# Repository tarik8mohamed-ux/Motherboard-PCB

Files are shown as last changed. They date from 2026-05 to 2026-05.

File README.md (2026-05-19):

# Hyperloop Motherboard PCB
Hyperloop Motherboard PCB Design (KiCad Schematics, component footprints, layouts, and diagrams)

Cornell Hyperloop SP'26
ECC:   Tarik, Peri, Farah, and Vinny

## Introduction: 
This project is a central control PCB designed to serve as the primary communication and motor control hub for Cornell Hyperloop's MiniPod. The board integrates multiple communication protocols to interface with a variety of peripherals: CANopen for servo motor control via the EPOS2 70/10, Step/Dir for stepper motor control via the TB6600, I2C for a distributed sensor network of temperature and current monitors, and PWM for fan speed control. The modular architecture supports hot-pluggable expansion, allowing sensors, MCU, and Multiplexers to be swapped or added without disrupting system operation. The board is ~265mm x 135mm and consists of 4 Layers: Signal-GND-PWR-Signal, with the PWR plane seperated into 3.3V,5.0V, and 12V sections to support different components. The most up to date files are in the Hyperloop Organized PCB folder.

Hyperloop PCB 3D View 2
Hyperloop PCB 3D View
Hyperloop PCB Planes View

## Components:
Cornell Hyperloop's MiniPod is ~7ft, meaning that sesnors and motors must be controlled by the motherbaord from a distance. This is why most components will be connected to the PCB via Cable/Wire connectors.
#### MCU:
The motherboard is controlled with an Arduino Nano R4
<table>
  <tr>
    <td align="center"><b>Arduino Nano R4</b></td>
  </tr>
  <tr>
    <td>1782_sml</td>
  </tr>
</table>

#### Sensors & Fan Control:
Overheating and current spikes are critical concerns on the Pod, so temperature and current sensors are distributed throughout. Temperature sensors use 8-pin Molex connectors (2 power, 2 communication, 1 interrupt, 3 alert pins), while current sensors use 4-pin Molex connectors (2 power, 2 communication pins). Vin+ and Vin− are connected across the points being measured, not the board, and I²C addresses are permanently hardset on the board. Additionally, a TCA9548A I2C multiplexer was integrated to expand the single I2C bus into up to 8 independent channels. 4-pin cooling fans are also distributed across the Pod, represented as 4-pin Molex connectors.
<table>
  <tr>
    <td align="center"><b>Temperature Sensor: MCP9808 </b></td>
    <td align="center"><b>Current Sensor: INA260</b></td>
    <td align="center"><b>Fan: Arctic P12</b></td>
    <td align="center"><b>Multiplexer: TCA9548A</b></td>
  </tr>
  <tr>
    <td></td>
    <td>1782_sml</td>
    <td>1782_sml</td>
    <td>1782_sml</td>
  </tr>
</table>

#### Motor Control:
The Pod interfaces with a TB6600 stepper driver and an EPOS2 70/10 servo controller. The TB6600 is controlled via Step/Dir/Enable signals through a Phoenix Contact screw terminal, and the EPOS2 communicates over CANopen through a Molex Micro-Fit 3.0 4-pin connector.
<table>
  <tr>
    <td align="center"><b>4-pin Pheonix Contact Screw Terminal</b></td>
    <td align="center"><b>Molex Micro-Fir 3.0 4-pin connector</b></td>
  </tr>
  <tr>
    <td></td>
    <td>1782_sml</td>
  </tr>
</table>

#### GPIO Expander:
An MCP23017 I2C expander is included to provide additional GPIO pins for the Pod as needed. Breakout headers expose all 16 I/O pins for flexible peripheral connections.
The motherboard is controlled with an Arduino Nano R4
<table>
  <tr>
    <td align="center"><b>MCP23017 I2C Expander:</b></td>
  </tr>
  <tr>
    <td>1782_sml</td>
  </tr>
</table>

#### Power, Resistors, Capacitors:
The PCB contains 3.3V,5.0V, and 12.0V sections in the power plane. XT30 connectors will be used to connect external battery packs to drive the power plane.
Resistors typically take on the role of pull-ups in this design. Through-Hole Resistors are used for ease of soldering. On the other hand, capacitors are typically used for bypass or decoupling. In this context, we picked SMD capacitors despite the extra difficulty in soldering because they significantly outperform THT.
<table>
  <tr>
    <td align="center"><b>XT30 Connector:</b></td>
  </tr>
  <tr>
    <td>1782_sml</td>
  </tr>
</table>

## Communication Systems:
### I2C Sensor Network & I2C Expander:
The I2C network, located in the top left of the PCB, is managed by a TCA9548A multiplexer which expands the microcontroller's single I2C bus into 4 independent channels, each with its own pull-up resistors to maintain signal integrity. Each channel hosts sensor peripherals, with every device supported by a dedicated decoupling capacitor for noise suppression. A series resistor on the main I2C line dampens inductive ringing before the signal reaches the multiplexer. MCP9808 temperature sensors feature an active-low alert pin connected to a microcontroller GPIO, enabling interrupt-driven temperature monitoring without continuous polling. An MCP23017 I2C I/O expander is also connected to the bus, currently populated with breakout headers for flexible future peripheral connections.

### CAN EPOS2 70/10:
CANopen communication is implemented using a TCAN332 transceiver, which converts the microcontroller's TX/RX signals into differential CANH/CANL signals. A 120Ω termination resistor is placed at the output connector to prevent signal reflections. The bus connects to an EPOS2 70/10 servo controller via a Molex Micro-Fit 3.0 cable. It is located below the MCU.

### Step/Dir TB6600:
The TB6600 stepper driver is controlled via three GPIO signals — PUL+, DIR+, and ENA+ — using a common-cathode wiring configuration. Series resistors on each line dampen signal ringing before reaching the Phoenix Contact screw terminal output connector. It is located just above the MCU.

### PWM Fan CTRL:
Two pairs of fans are controlled via PWM signals from the microcontroller, with each pair sharing a single PWM output to conserve GPIO pins. One tachometer signal per pair is routed back to a microcontroller GPIO, providing RPM feedback for monitoring fan speed. Each fan connector includes dedicated power and ground connections for reliable operation. It is located on the right side of the board.

## Future Updates
-INA260 Alert Pin: The INA260 current sensor connector will be expanded from 4 to 5 pins to expose the ALERT pin, enabling interrupt-driven current monitoring in place of polling across the I2C channels and significantly improving CPU efficiency.    

-TCAN332 Connector Orientation: The CAN connector will be changed from horizontal to vertical to improve accessibility and PCB layout clarity.

-Component Density: Component placement will be optimized for a smaller board footprint, reducing fabrication cost.

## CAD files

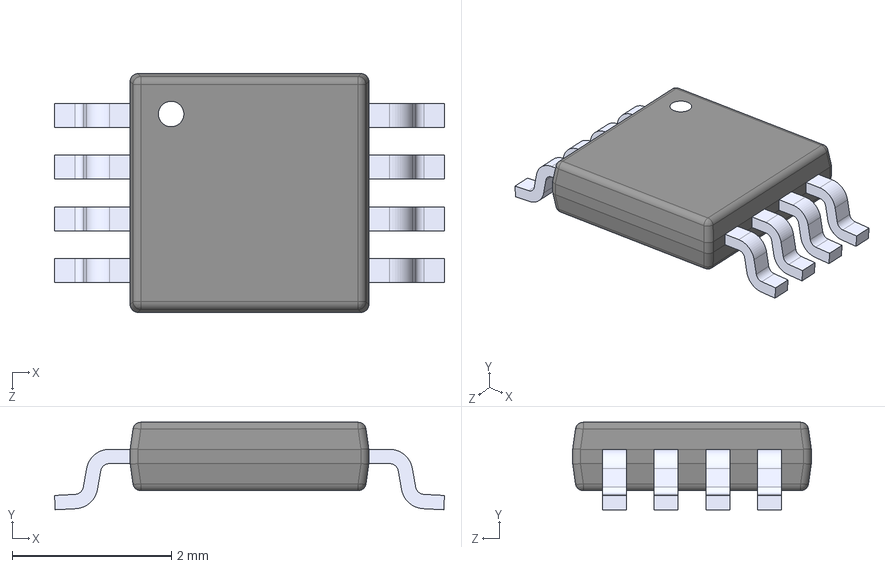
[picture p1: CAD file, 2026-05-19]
KiCad Components/KiCad 3D Models/LTC4446EMS8EPBF(MagBrake Driver).step
4.90 x 1.10 x 3.00 mm

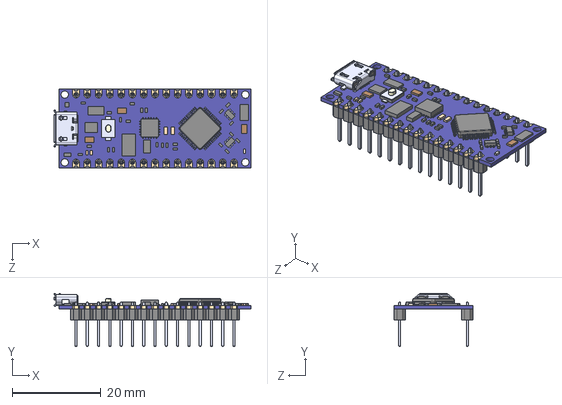
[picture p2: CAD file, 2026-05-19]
KiCad Components/KiCad 3D Models/Arduino_Nano_Every.STEP
44.3 x 12.0 x 17.8 mm

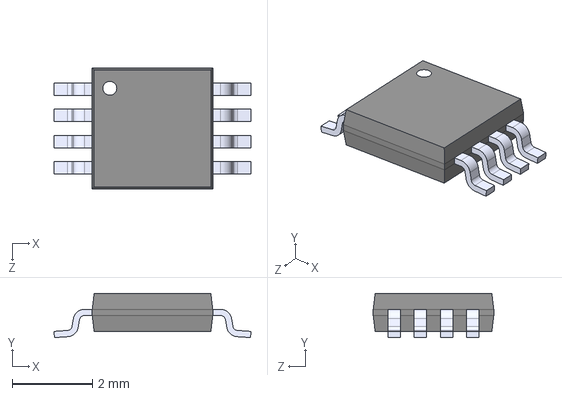
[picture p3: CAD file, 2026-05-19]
KiCad Components/KiCad 3D Models/MCP9808-E_MS(Temp Sensor).step
4.90 x 1.10 x 3.00 mm

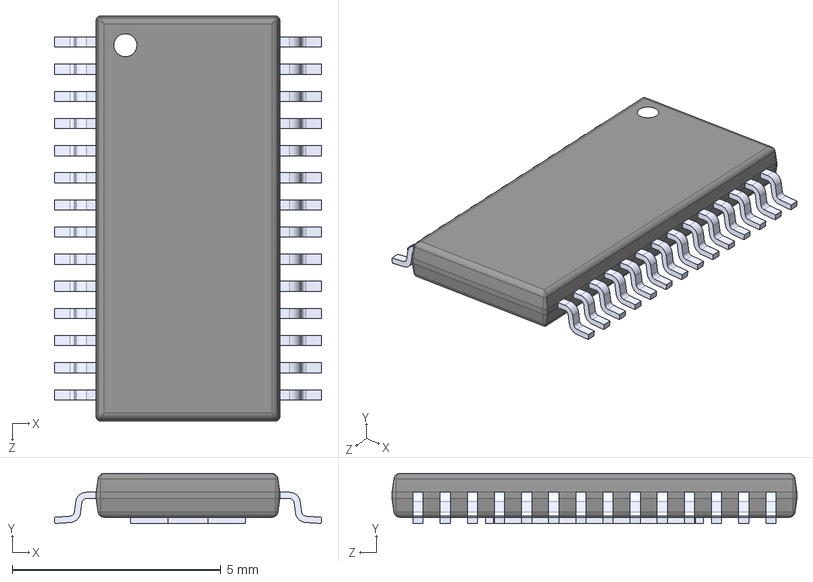
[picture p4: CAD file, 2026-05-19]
KiCad Components/KiCad 3D Models/DRV8424PWPR(Motor Driver).step
6.40 x 1.20 x 9.70 mm

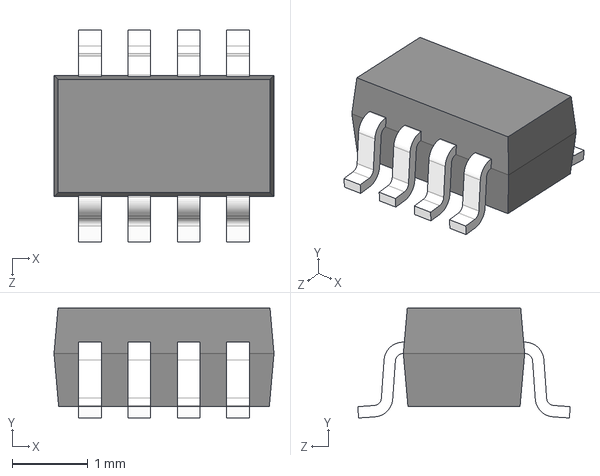
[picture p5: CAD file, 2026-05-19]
KiCad Components/KiCad 3D Models/INA219(Current Sensor).step
2.90 x 1.45 x 2.80 mm

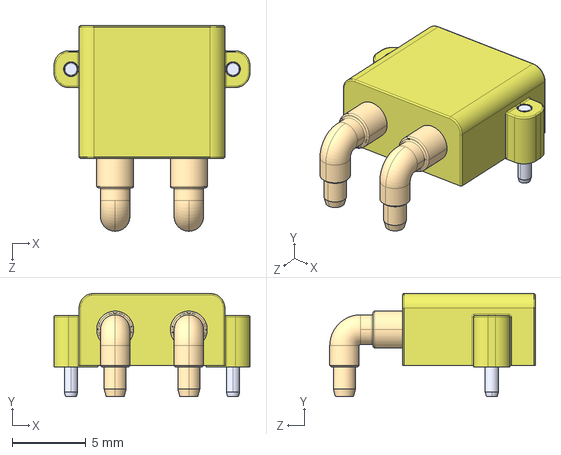
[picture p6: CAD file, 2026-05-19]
KiCad Components/KiCad 3D Models/XT30PW-M.step
13.3 x 7.00 x 14.0 mm

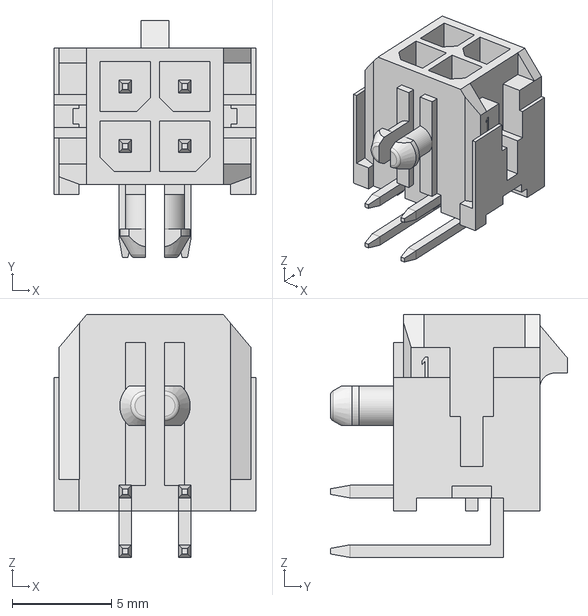
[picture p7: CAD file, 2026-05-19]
KiCad Components/KiCad 3D Models/TCAN_Connector(Horizontal).stp
10.2 x 11.9 x 12.2 mm

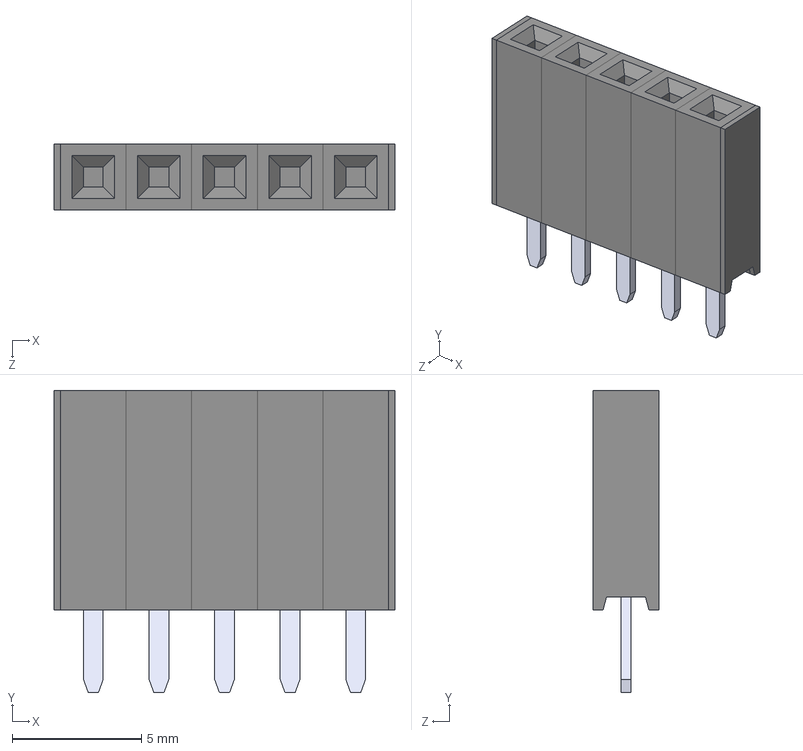
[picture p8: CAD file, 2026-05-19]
KiCad Components/KiCad 3D Models/5FemaleHeaderPins.STEP
13.2 x 11.7 x 2.54 mm
PPPC021LFBN-RC_C05
Pin - Tin x 5

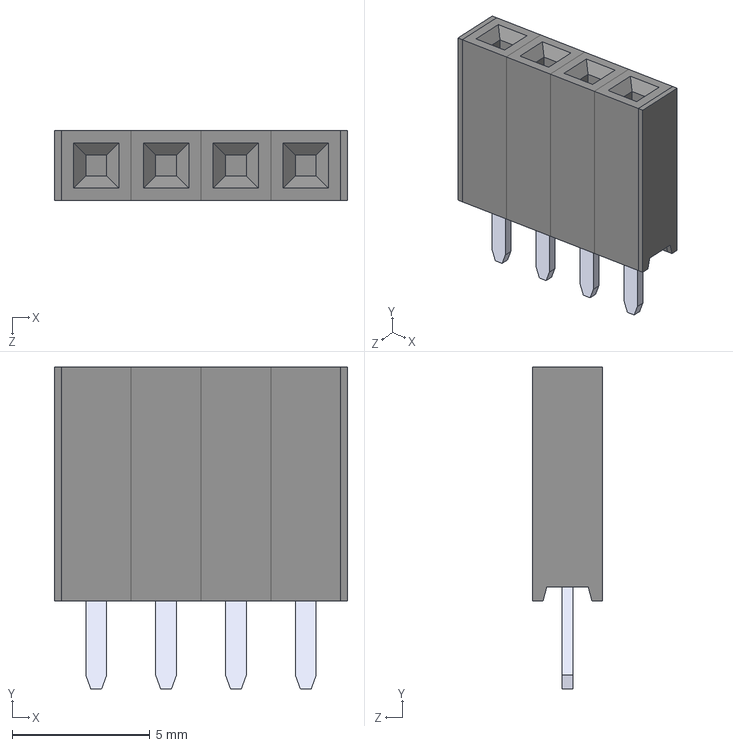
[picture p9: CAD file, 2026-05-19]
KiCad Components/KiCad 3D Models/4FemaleHeaderPins.STEP
10.7 x 11.7 x 2.54 mm
PPPC021LFBN-RC_C04
Pin - Tin x 4

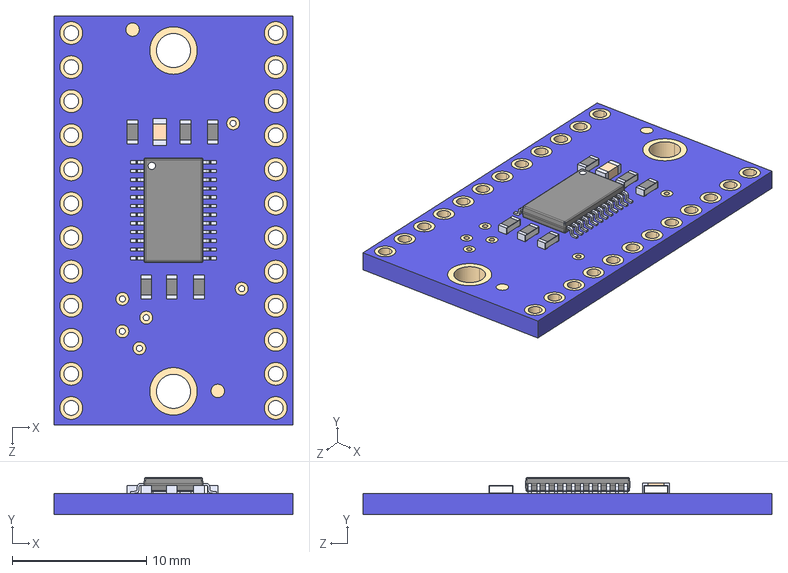
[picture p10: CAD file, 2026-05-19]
KiCad Components/KiCad 3D Models/TCA9548APWR(Multiplexer_BreakoutBoard).step
17.8 x 2.77 x 30.5 mm
TCA9548APWR_TCA9548APWR

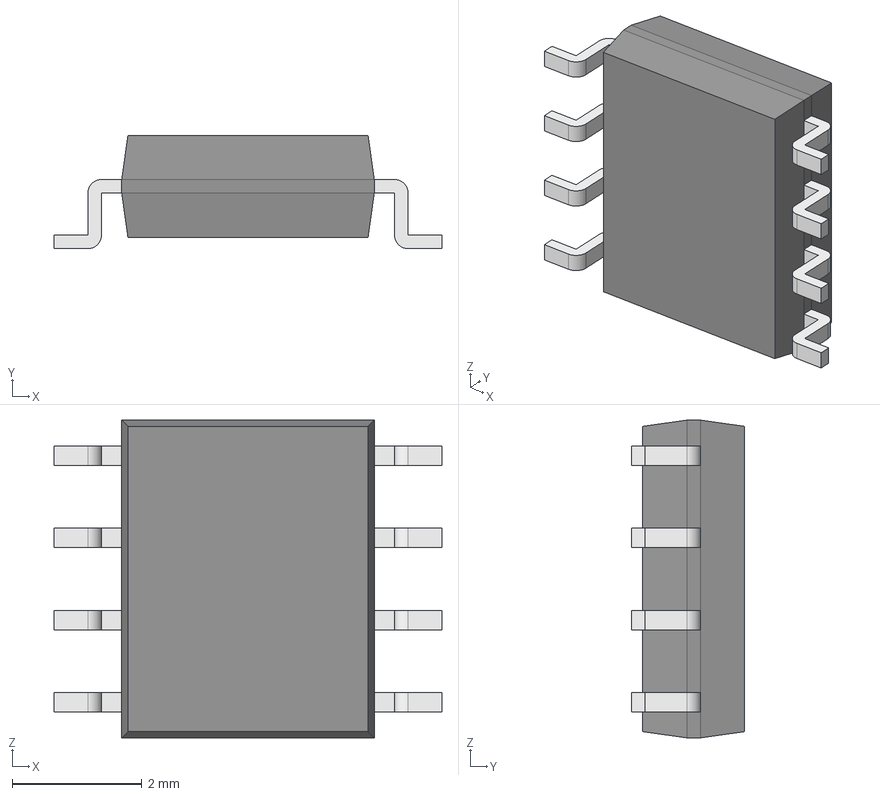
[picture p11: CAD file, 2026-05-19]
KiCad Components/KiCad 3D Models/TCAN332DR.step
5.99 x 1.75 x 4.91 mm
Body001 (Mirror #1) x 4
XY-plane x 12
X-axis x 12

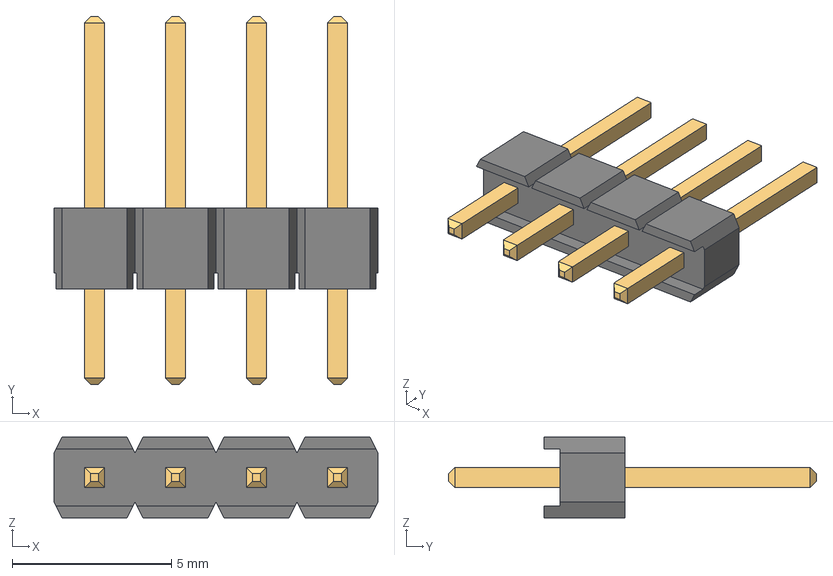
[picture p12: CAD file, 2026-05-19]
KiCad Components/KiCad 3D Models/4MaleHeaderPins.stp
10.2 x 11.5 x 2.54 mm
6130xx11121_PIN x 4

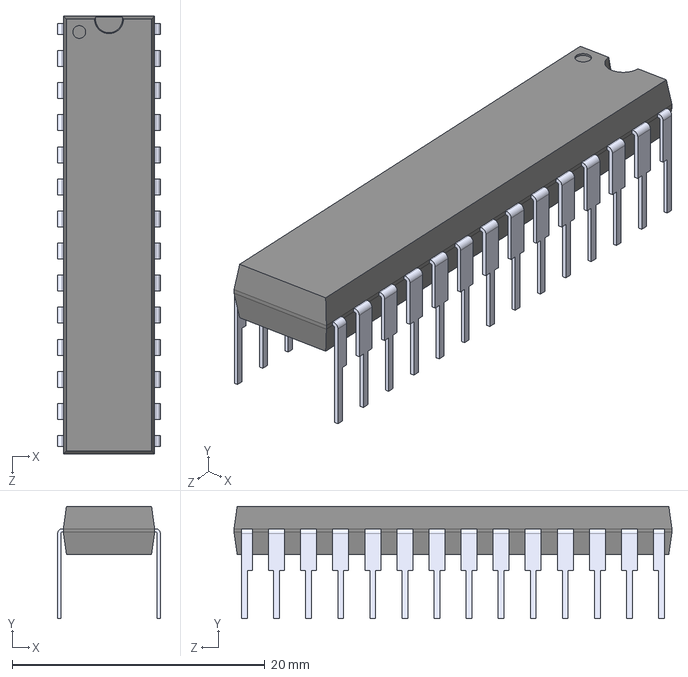
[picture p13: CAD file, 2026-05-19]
KiCad Components/KiCad 3D Models/MCP23017-E_SP(IO Expander).step
8.13 x 8.89 x 34.7 mm

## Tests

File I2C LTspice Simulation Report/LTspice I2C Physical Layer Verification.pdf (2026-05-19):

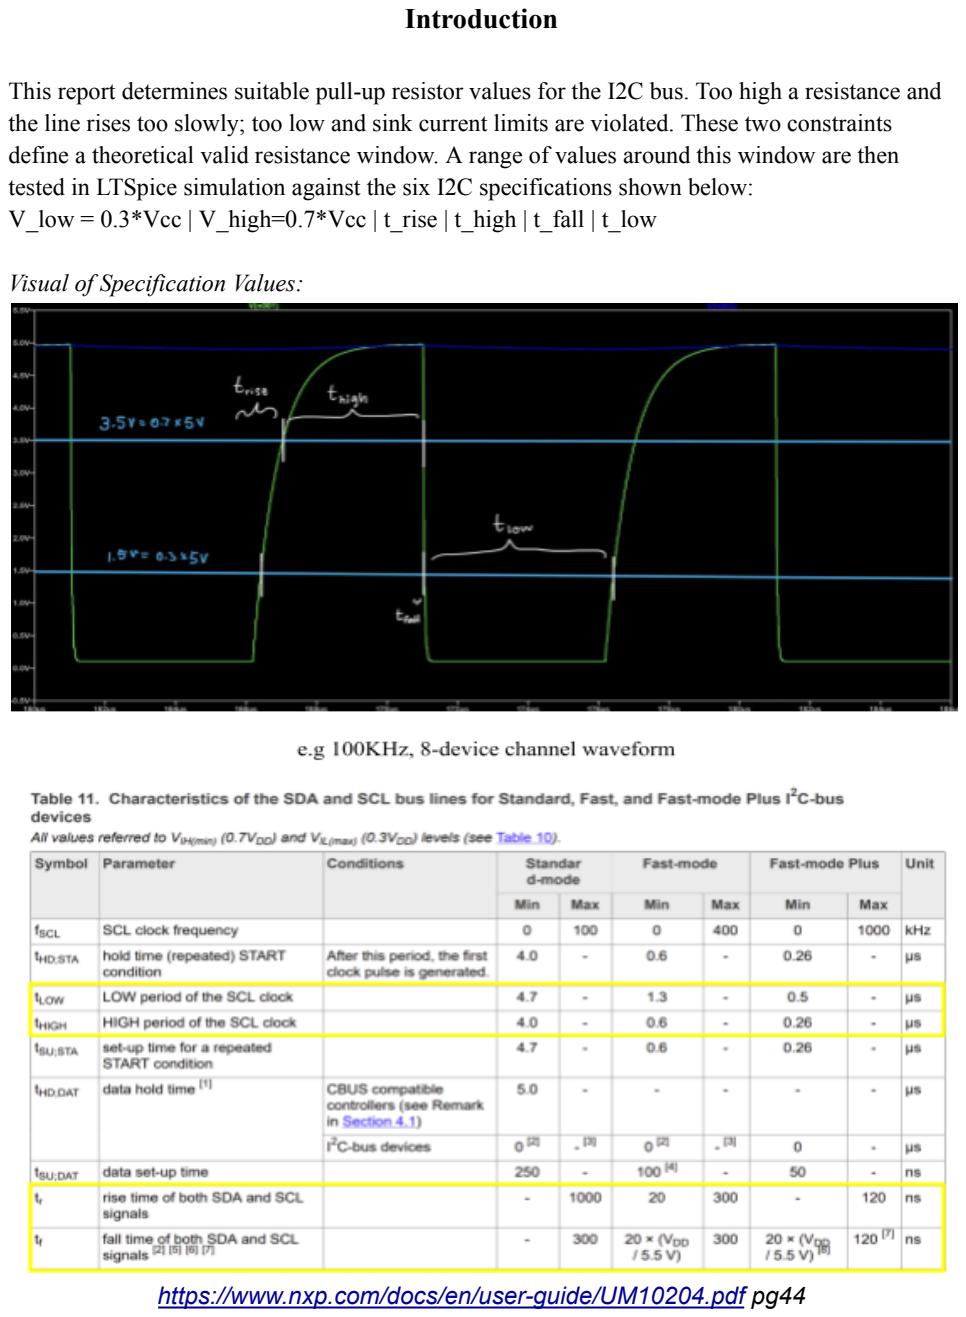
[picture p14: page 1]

Introduction

This report determines suitable pull-up resistor values for the I2C bus. Too high a resistance and the line rises too slowly; too low and sink current limits are violated. These two constraints define a theoretical valid resistance window. A range of values around this window are then tested in LTSpice simulation against the six I2C specifications shown below:
V_low = 0.3*Vcc | V_high=0.7*Vcc | t_rise | t_high | t_fall | t_low

Visual of Specification Values:

https://www.nxp.com/docs/en/user-guide/UM10204.pdf pg44

Limit to I Communication Speed

2
C

The maximum operating frequency of an I²C bus is reached when the design constraints on the pull-up resistors conflict—specifically, when the minimum pull-up resistance required for reliable logic-level operation becomes larger than the maximum pull-up resistance allowed to meet timing requirements.

The minimum pull-up resistance R is set by the need to ensure that devices can pull the line min low without exceeding their maximum sink current. It is given by:

R

min =

V

DD− V
OL(max)
I
OL(max)
This ensures that when a device drives the line low, the resulting voltage does not exceed the maximum allowable low-level voltage V .
OL(max)
The maximum pull-up resistance R is determined by the requirement that the signal rise max time is fast enough to meet the bus timing specifications. Since the rising edge is governed by the RC time constant of the pull-up resistor and bus capacitance, it is approximated by:

R

max =

t
rise
0.8473 * C
b
where t | is the maximum allowable rise time and | is the total bus capacitance.
rise

C
b
As the desired communication frequency increases, the allowable rise time t decreases, which
rise
in turn lowers R | . The system reaches its maximum feasible speed when | > | , at max
R
min

R
max
which point no resistor value can simultaneously satisfy both the current-driving and timing constraints.

I2C Bus Values Base Assumptions

Characteristic | Value | Known/Assumption
8-device channel Bus Capacitance(C ) b | 200pF | Assumption
4-device channel Bus Capacitance(C ) b | 160pF | Assumption
Bus High Voltage(V ) cc | 5.0V | Known
Sensors’ Sink Current(I ) OL | 3mA | Known
Sensors’ Voltage Output Low (V ) OL | 0.4V | Known
- Based on the MCP9808 Datasheet(pg4), (https://ww1.microchip.com/downloads/en/DeviceDoc/MCP9808-0.5C-Maximum-Accuracy-Digital-Temperature-Sensor-Data-Sheet-DS20005095B.pdf) V = 0.4V and | =3mA. It adds a capacitance
OL
I | OL
of 5pF to the bus line.
- Based on the INA260 Datasheetpg(7) (https://www.ti.com/lit/ds/symlink/ina260.pdf?ts=1776970295509) V = 0.4V and =3mA. It adds a capacitance of
OL

I
OL
3pF to the bus line.
- Based on the TCA9548A Datasheetpg(6) (https://www.ti.com/lit/ds/symlink/tca9548a.pdf?ts=1776969785007) V = 0.4V and | =3mA. It adds a capacitance
OL | I OL
of ~28pF-36pF to the bus line. Assume a worst case of ~36pF.
- Based on this Wire Capacitance Calculator, (https://www.emisoftware.com/calculator/wire-over-ground-plane-capacitance/) using r = 0.01in(24AWG wire), h = 12in, L=1m, ε=1, the capacitance of each wire is ~7.1pF.
- Based on this Wire Inductance Calculator, (https://www.allaboutcircuits.com/tools/wire-self-inductance-calculator/) using d=0.02in(24AWG wire), L=36in, the inductance of each wire is ~1.5uH.

C
b

≈ C

bus sensor + C

wire + C

mux + C
extra, just in case

8-device Channel Temperature Sensor:
C
b

≈ 8(5pF) + 8(7. 1pF) + 36pF + 70pF = 202. 8pF

4-device Channel Current Sensor:
C

b≈ 4(3pF) + 4(7. 1pF) + 36pF + 70pF = 146. 4pF

Theoretical Max/Min Pullup Resistor Values

R(min) =

V

cc−V
OL
I
OL(max)

=

5−0.4
3*10

−3 Ω = 1533Ω
Standard Mode(100KHz):(t | ) rise(max) = 1000ns
8-device channel:
R(max) =

t
rise
0.8473 * C
b

=

| (1000*10 −9 ) 0.8473 * (200*10 −12)
= 5. 9kΩ
4-device channel:
R(max)=

t
rise
0.8473 * C
b

=

| (1000*10 −9 ) 0.8473 * (160*10 −12)
= 7. 38kΩ
Fast-Mode(400KHz) :(t | )
rise(max) = 300ns
8-device channel:
R(max)=

t
rise
0.8473 * C
b

=

| (300*10 −9 ) 0.8473 * (200*10 −12)
= 1. 77kΩ
4-device channel:
R(max)=

t
rise
0.8473 * C
b

=

| (300*10 −9 ) 0.8473 * (160*10 −12)
= 2. 2kΩ
Fast-Mode Plus(1MHz): (t | )
rise(max) = 120ns
8-device channel:
R(max)=

t
rise
0.8473 * C
b

=

| (120*10 −9 ) 0.8473 * (200*10 −12)
= 708Ω
4-device channel:
R(max)=

t
rise
0.8473 * C
b

=

| (300*10 −9 ) 0.8473 * (160*10 −12)
= 885Ω

This Desmos model can be used to find the average power dissipation based of the value of pullup resistors, bus capacitance, frequency of communication, and duty cycle:
Power Dissipation Graph (https://www.desmos.com/calculator/b0qhnq1roh)
Default Values: (V=5V, D=0.4, f=100kHz, C=200pF)
Note: P(R) = 2 * Expression . Expression is multiplied by 2 to account for cumulative power dissipation of both SCL and SDA lines.

Conclusion:
The I²C communication breaks down when operating in Fast-Mode Plus(1MHz) because 708,885Ω > 1533Ω . Fast Mode(400kHz) is the fastest reliable communication speed.

LTspice Simulation of I²C Bus

Introduction:

This report documents an LTspice simulation of an I2C bus network used to verify signal integrity and timing compliance for a system in which a microcontroller communicates outward to sixteen peripheral devices through a single TCA9548A 8-channel multiplexer. The devices under simulation are the MCP9808 temperature sensor and the INA260 current and power monitor.

Because manufacturer-provided SPICE models are not available for any of the integrated circuits in this system, all components are represented using behavioral approximations constructed from their published electrical characteristics.

The system operates at a supply voltage of 5 V. Pull-up resistors will be selected to balance rise time performance against sink current requirements under the total capacitive load presented by the network.

Circuit Model:
The I2C bus is modeled as a passive electrical network in LTSpice, scoped to the physical layer only. No active device logic, protocol sequencing, or acknowledgment behavior is included.

SCL line — Modeled as a voltage-controlled switch to ground driven by a pulse source, replicating the open-drain behavior of I2C. The switch pulls SCL low when closed and releases it to the pull-up when open. The PULSE settings model the specific frequency the line is modeled at. SDA is modeled identically.

Mux channels — The TCA9548A is represented as three independently controlled switches, one per active channel, each driven by a non-overlapping pulse source.

Sensors — Each device pin is modeled as a 10pF capacitor to ground. This is appropriate for a physical layer simulation since an I2C input pin presents primarily a capacitive load during passive reception.

Pull-up resistors — The main upstream line and each downstream mux channel carry a dedicated pull-up resistor to 5V.

Wire model — Each wire run is represented as a pi-section lumped network — shunt capacitance at each end with series resistance and inductance between them — realistically capturing the distributed parasitics of 1–3ft wire runs without requiring a full transmission line model.

Series damping resistor — A resistor placed in series with the main bus line suppresses inductive ringing on fast falling edges by damping the LC resonance formed by wire inductance

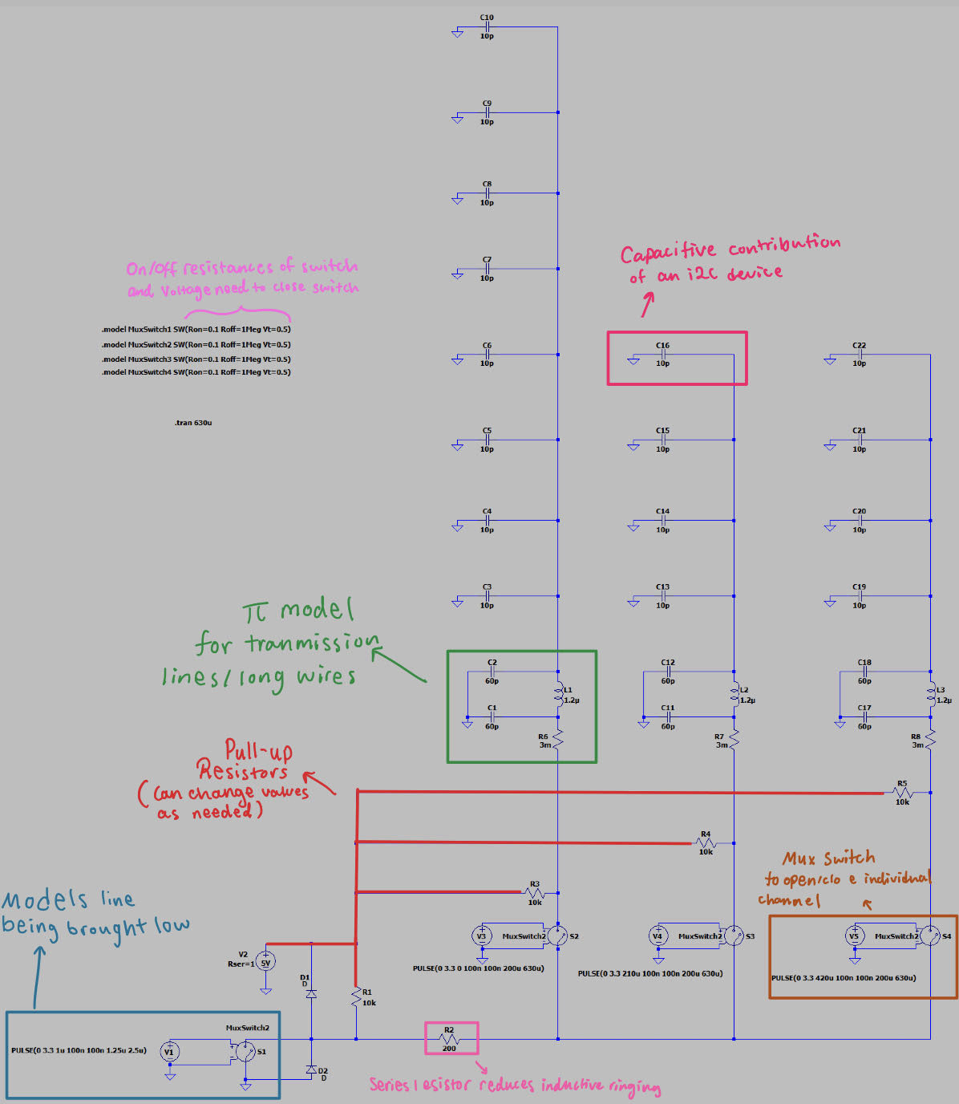
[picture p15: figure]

PULSE(V
low

, V
ℎigℎ

, Delay, Rise Time, T
on

, Period)

V2,V3,V4 are set to PULSE(0, 3.3, X, 100n, 200u, 630u) with delay(X) being different for each so no two channels are opened at the same time.

Data & Findings

The following simulations have fixed values R1 = 10kΩ , R2 = 200Ω. Total pull-up resistance can be found on this Calculator. (https://www.desmos.com/calculator/jdodsuhifn)

Data Collection for simulations can be found on this Spreadsheet. (https://docs.google.com/spreadsheets/d/1wfCMvmyPzd3MK7duu8wWSZKmwc6TmVF-cgnBPVn-W_I/edit?gid=0#gid=0)

Standard Mode(100KHz):

The following settings will be used to model the limit of 100kHz communication speed:

- V1: PULSE(0, 3.3, 1u, 100n, 5u, 10u)
“0-3.3V, delay 1u before it starts pulsing, it takes 100n to change from 0-3.3V, it is 3.3V for 5u with a period of 10u

Finding:
- 8-device channel Highest resistance that all specifications were met: R2 = 14kΩ(total pullup resistance of ~5.87kΩ)
- 4-device channel Highest resistance that all specifications were met: R3 = 20kΩ(total pullup resistance of ~7.2kΩ)

Fast-Mode(400KHz):

The following settings will be used to model the limit of 400kHz communication speed:

- V1: PULSE(0, 3.3, 1u, 100n, 1.25u, 2.5u)
“0-3.3V, delay 1u before it starts pulsing, it takes 100n to change from 0-3.3V, it is 3.3V for 1.25u with a period of 2.5u

Finding:
- 8-device channel Highest resistance that all specifications were met: R2 = 2.1kΩ(total pullup resistance of ~1.87kΩ)

- 4-device channel Highest resistance that all specifications were met: R3 = 2.5kΩ(total pullup resistance of ~2.1kΩ)

Conclusion

The I2C bus will use a 10kOhm on the mcu side of the multiplexer for each line. A 200Ohm resistor will be in series with the bus to reduce ringing. Operating the 8-device channel’s pullup resistor at 2kOhm( total resistance of 1.8kOhm), and the 4-device channel’s pullup at 2.2kOhm(total resistance of 1.94kOhm) allow for both 100kHz and 400kHz I2C communication specification to be met in simulation.

Main Sources:
Information for Resistor Max/Min: TI paper (https://www.ti.com/lit/an/slva689/slva689.pdf?ts=1776536101655)
Specification Terms Meaning: Analog Devices page: (https://www.analog.com/en/resources/technical-articles/i2c-timing-definition-and-specification-guide-part-2.html) Specification tested in Simulation: I2C Specification (https://www.nxp.com/docs/en/user-guide/UM10204.pdf)

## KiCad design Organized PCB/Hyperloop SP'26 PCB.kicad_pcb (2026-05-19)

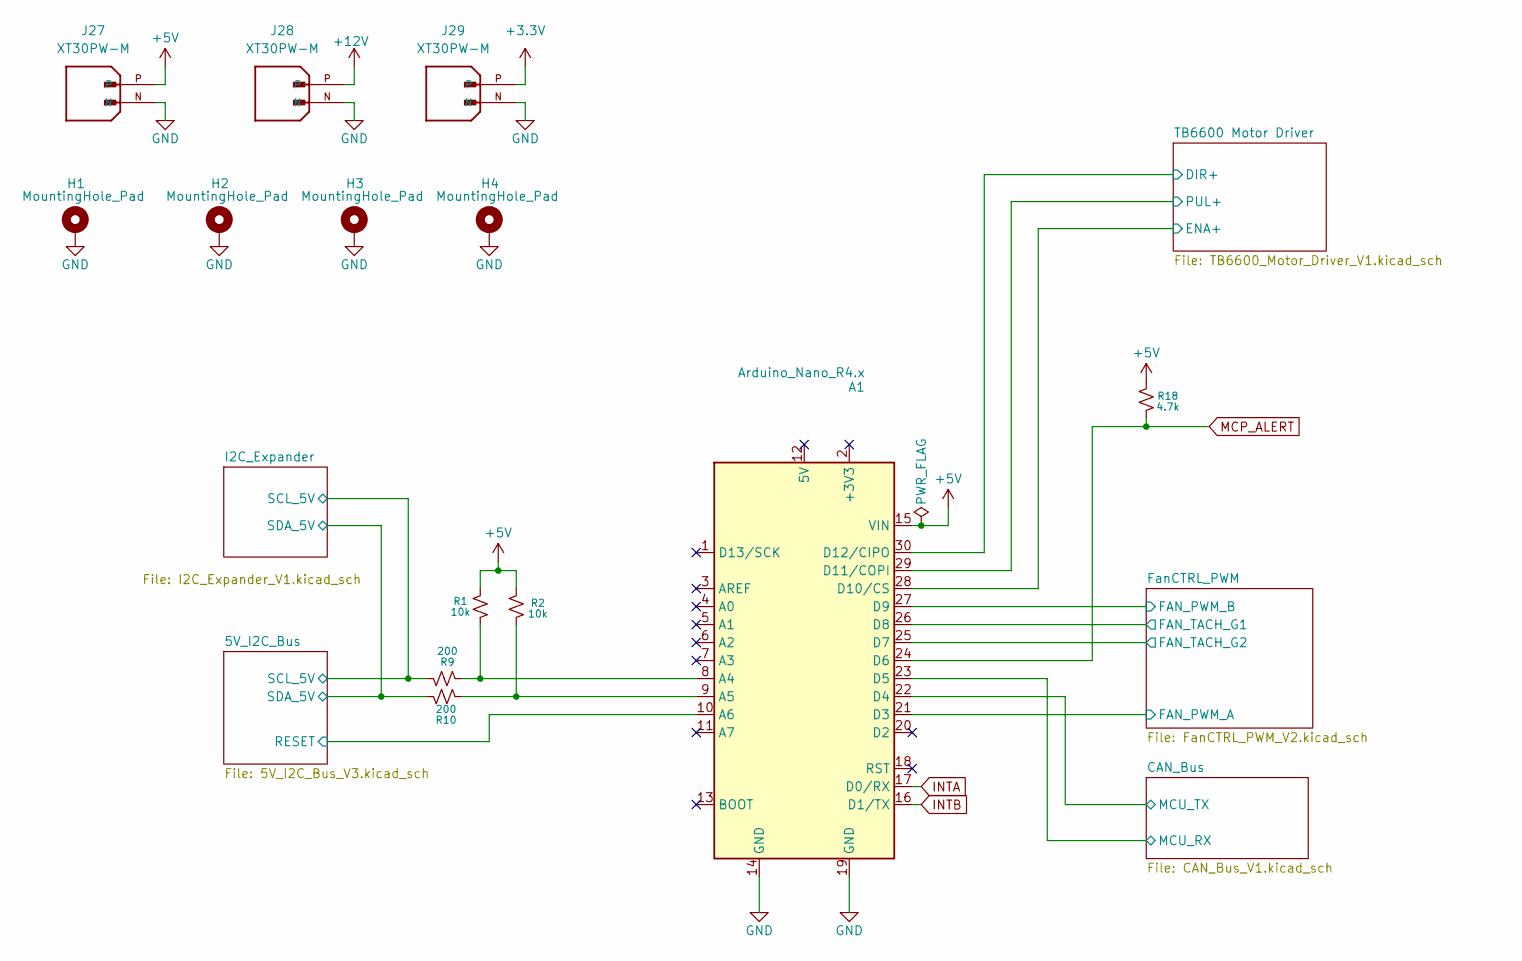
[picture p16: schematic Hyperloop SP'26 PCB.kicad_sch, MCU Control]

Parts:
A1: Arduino_Nano_R4.x; Arduino_Nano
H1, H2, H3, H4: MountingHole_Pad; MountingHole_3.2mm_M3_Pad_TopBottom
J27, J28, J29: XT30PW-M; AMASS_XT30PW-M; PARTREV 1.2
R1, R2: 10k; R_Axial_DIN0207_L6.3mm_D2.5mm_P7.62mm_Horizontal
R9, R10: 200; R_Axial_DIN0207_L6.3mm_D2.5mm_P7.62mm_Horizontal
R18: 4.7k; R_Axial_DIN0207_L6.3mm_D2.5mm_P7.62mm_Horizontal

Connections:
+3.3V: J29.P; also elsewhere on the board
+5V: A1.15 (VIN), J27.P, R1.2, R2.2, R18.2; also elsewhere on the board
+12V: J28.P; also elsewhere on the board
/5V_I2C_Bus/RESET: A1.10 (A6); also elsewhere on the board
/5V_I2C_Bus/SCL_5V: R9.2; also elsewhere on the board
/5V_I2C_Bus/SDA_5V: R10.2; also elsewhere on the board
/CAN_Bus/MCU_RX: A1.23 (D5); also elsewhere on the board
/CAN_Bus/MCU_TX: A1.22 (D4); also elsewhere on the board
/FanCTRL_PWM/FAN_PWM_A: A1.21 (D3); also elsewhere on the board
/FanCTRL_PWM/FAN_PWM_B: A1.27 (D9); also elsewhere on the board
/FanCTRL_PWM/FAN_TACH_G1: A1.26 (D8); also elsewhere on the board
/FanCTRL_PWM/FAN_TACH_G2: A1.25 (D7); also elsewhere on the board
/TB6600 Motor Driver/DIR+: A1.30 (D12/CIPO); also elsewhere on the board
/TB6600 Motor Driver/ENA+: A1.28 (D10/CS); also elsewhere on the board
/TB6600 Motor Driver/PUL+: A1.29 (D11/COPI); also elsewhere on the board
GND: A1.14 (GND), A1.19 (GND), H1.1, H2.1, H3.1, H4.1, J27.N, J28.N, J29.N; also elsewhere on the board
INTA: A1.17 (D0/RX); also elsewhere on the board
INTB: A1.16 (D1/TX); also elsewhere on the board
MCP_ALERT: A1.24 (D6), R18.1; also elsewhere on the board
unnamed: A1.8 (A4), R1.1, R9.1
unnamed: A1.9 (A5), R2.1, R10.1

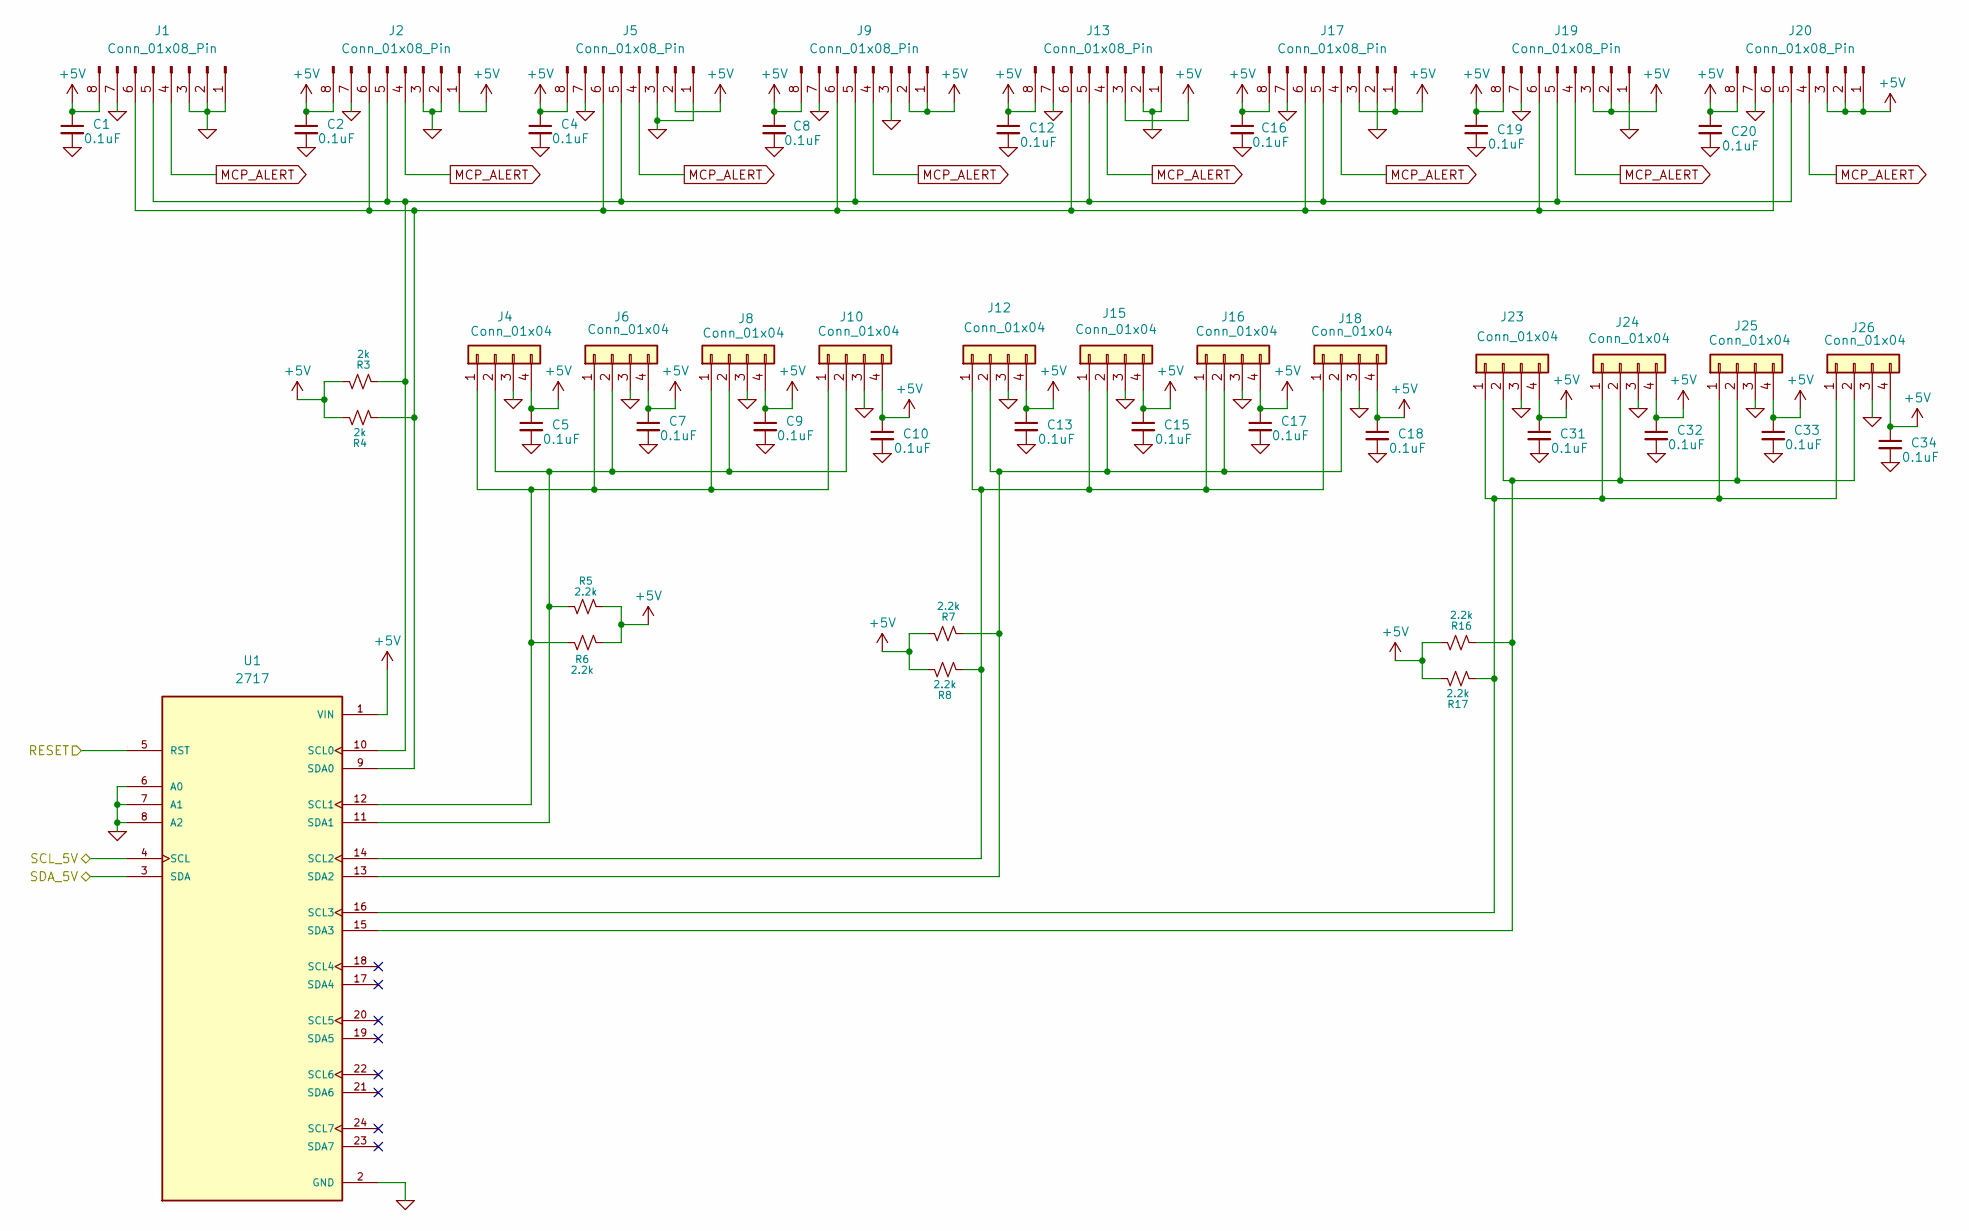
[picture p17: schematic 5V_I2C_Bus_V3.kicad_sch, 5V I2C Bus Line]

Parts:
C1, C2, C4, C5, C7, C8, C9, C10, C12, C13, C15, C16, C17, C18, C19, C20, C31, C32, C33, C34: 0.1uF; C_0805_2012Metric
J1, J2, J5, J9, J13, J17, J19, J20: Conn_01x08_Pin; Molex_KK-254_AE-6410-08A_1x08_P2.54mm_Vertical
J4, J6, J8, J10, J12, J15, J16, J18, J23, J24, J25, J26: Conn_01x04; Molex_KK-254_AE-6410-04A_1x04_P2.54mm_Vertical
R3, R4: 2k; R_Axial_DIN0207_L6.3mm_D2.5mm_P7.62mm_Horizontal
R5, R6, R7, R8, R16, R17: 2.2k; R_Axial_DIN0207_L6.3mm_D2.5mm_P7.62mm_Horizontal
U1: 2717; MODULE_2717; PARTREV Sep 11, 2015

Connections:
+5V: C1.1, C2.1, C4.1, C5.1, C7.1, C8.1, C9.1, C10.1, C12.1, C13.1, C15.1, C16.1, C17.1, C18.1, C19.1, C20.1, C31.1, C32.1, C33.1, C34.1, J1.8, J2.1, J2.8, J4.4, J5.2, J5.8, J6.4, J8.4, J9.1, J9.2, J9.8, J10.4, J12.4, J13.3, J13.8, J15.4, J16.4, J17.1, J17.3, J17.8, J18.4, J19.2, J19.3, J19.8, J20.1, J20.2, J20.3, J20.8, J23.4, J24.4, J25.4, J26.4, R3.2, R4.2, R5.2, R6.2, R7.2, R8.2, R16.2, R17.2, U1.1 (VIN); also elsewhere on the board
/5V_I2C_Bus/RESET: U1.5 (RST); also elsewhere on the board
/5V_I2C_Bus/SCL_5V: U1.4 (SCL); also elsewhere on the board
/5V_I2C_Bus/SDA_5V: U1.3 (SDA); also elsewhere on the board
GND: C1.2, C2.2, C4.2, C5.2, C7.2, C8.2, C9.2, C10.2, C12.2, C13.2, C15.2, C16.2, C17.2, C18.2, C19.2, C20.2, C31.2, C32.2, C33.2, C34.2, J1.1, J1.2, J1.3, J1.7, J2.2, J2.3, J2.7, J4.3, J5.1, J5.3, J5.7, J6.3, J8.3, J9.3, J9.7, J10.3, J12.3, J13.1, J13.2, J13.7, J15.3, J16.3, J17.2, J17.7, J18.3, J19.1, J19.7, J20.7, J23.3, J24.3, J25.3, J26.3, U1.2 (GND), U1.6 (A0), U1.7 (A1), U1.8 (A2); also elsewhere on the board
MCP_ALERT: J1.4, J2.4, J5.4, J9.4, J13.4, J17.4, J19.4, J20.4; also elsewhere on the board
unnamed: J1.5, J2.5, J5.5, J9.5, J13.5, J17.5, J19.5, J20.5, R3.1, U1.10 (SCL0)
unnamed: J1.6, J2.6, J5.6, J9.6, J13.6, J17.6, J19.6, J20.6, R4.1, U1.9 (SDA0)
unnamed: J4.1, J6.1, J8.1, J10.1, R6.1, U1.12 (SCL1)
unnamed: J4.2, J6.2, J8.2, J10.2, R5.1, U1.11 (SDA1)
unnamed: J12.1, J15.1, J16.1, J18.1, R8.1, U1.14 (SCL2)
unnamed: J12.2, J15.2, J16.2, J18.2, R7.1, U1.13 (SDA2)
unnamed: J23.1, J24.1, J25.1, J26.1, R17.1, U1.16 (SCL3)
unnamed: J23.2, J24.2, J25.2, J26.2, R16.1, U1.15 (SDA3)

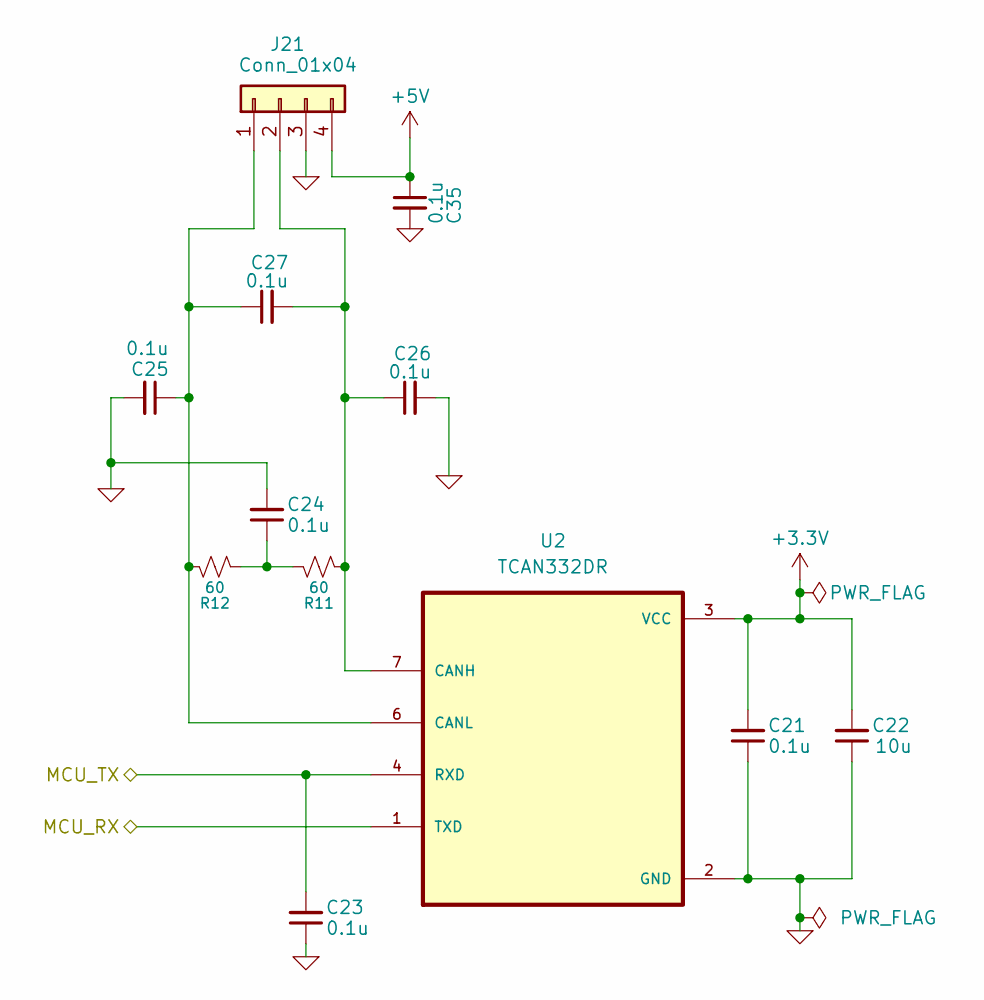
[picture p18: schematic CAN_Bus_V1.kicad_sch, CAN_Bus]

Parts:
C21, C23, C24, C25, C26, C27, C35: 0.1u; C_0805_2012Metric
C22: 10u; C_0805_2012Metric
J21: Conn_01x04; Molex_Micro-Fit_3.0_43045-0400_2x02_P3.00mm_Horizontal
R11, R12: 60; R_Axial_DIN0207_L6.3mm_D2.5mm_P7.62mm_Horizontal
U2: TCAN332DR; SOIC127P599X175-8N(TCAN332DR)

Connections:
+3.3V: C21.2, C22.2, U2.3 (VCC); also elsewhere on the board
+5V: C35.1, J21.4; also elsewhere on the board
/CAN_Bus/MCU_RX: U2.1 (TXD); also elsewhere on the board
/CAN_Bus/MCU_TX: C23.2, U2.4 (RXD); also elsewhere on the board
GND: C21.1, C22.1, C23.1, C24.2, C25.2, C26.2, C35.2, J21.3, U2.2 (GND); also elsewhere on the board
unnamed: C24.1, R11.2, R12.1
unnamed: C25.1, C27.1, J21.1, R12.2, U2.6 (CANL)
unnamed: C26.1, C27.2, J21.2, R11.1, U2.7 (CANH)

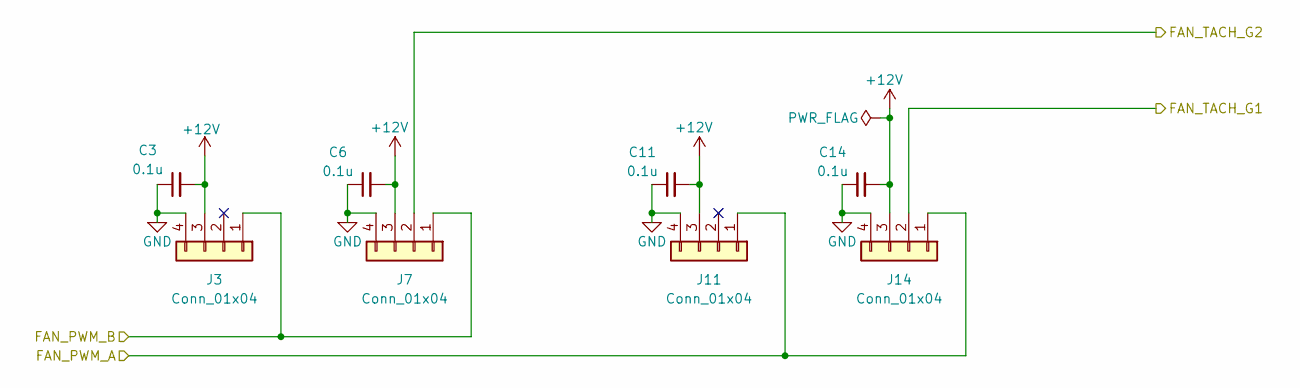
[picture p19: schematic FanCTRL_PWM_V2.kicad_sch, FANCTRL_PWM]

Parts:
C3, C6, C11, C14: 0.1u; C_0805_2012Metric
J3, J7, J11, J14: Conn_01x04; Molex_KK-254_AE-6410-04A_1x04_P2.54mm_Vertical

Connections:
+12V: C3.2, C6.2, C11.2, C14.2, J3.3, J7.3, J11.3, J14.3; also elsewhere on the board
/FanCTRL_PWM/FAN_PWM_A: J11.1, J14.1; also elsewhere on the board
/FanCTRL_PWM/FAN_PWM_B: J3.1, J7.1; also elsewhere on the board
/FanCTRL_PWM/FAN_TACH_G1: J14.2; also elsewhere on the board
/FanCTRL_PWM/FAN_TACH_G2: J7.2; also elsewhere on the board
GND: C3.1, C6.1, C11.1, C14.1, J3.4, J7.4, J11.4, J14.4; also elsewhere on the board

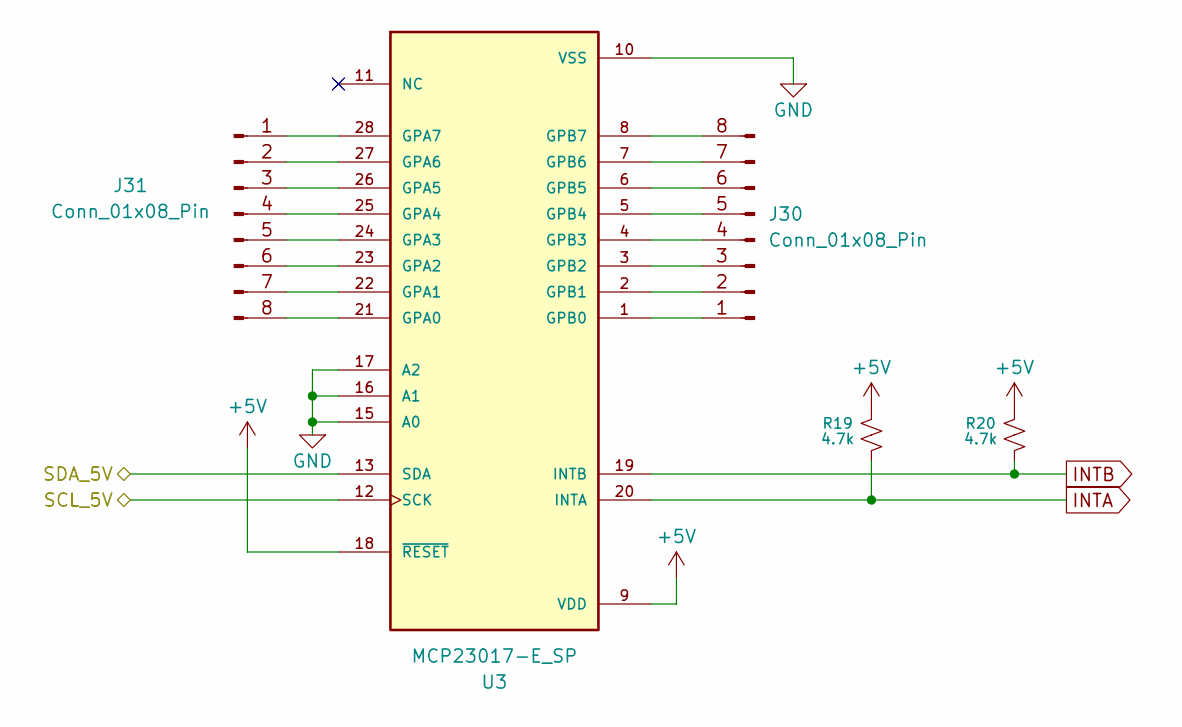
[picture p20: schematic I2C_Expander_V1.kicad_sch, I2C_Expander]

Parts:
J30, J31: Conn_01x08_Pin; PinHeader_1x08_P2.54mm_Vertical
R19, R20: 4.7k; R_Axial_DIN0207_L6.3mm_D2.5mm_P7.62mm_Horizontal
U3: MCP23017-E_SP; MCP23017(IO Expander); PARTREV D

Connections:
+5V: R19.1, R20.1, U3.9 (VDD), U3.18 (~RESET); also elsewhere on the board
/5V_I2C_Bus/SCL_5V: U3.12 (SCK); also elsewhere on the board
/5V_I2C_Bus/SDA_5V: U3.13 (SDA); also elsewhere on the board
GND: U3.10 (VSS), U3.15 (A0), U3.16 (A1), U3.17 (A2); also elsewhere on the board
INTA: R19.2, U3.20 (INTA); also elsewhere on the board
INTB: R20.2, U3.19 (INTB); also elsewhere on the board
unnamed: J30.1, U3.1 (GPB0)
unnamed: J30.2, U3.2 (GPB1)
unnamed: J30.3, U3.3 (GPB2)
unnamed: J30.4, U3.4 (GPB3)
unnamed: J30.5, U3.5 (GPB4)
unnamed: J30.6, U3.6 (GPB5)
unnamed: J30.7, U3.7 (GPB6)
unnamed: J30.8, U3.8 (GPB7)
unnamed: J31.1, U3.28 (GPA7)
unnamed: J31.2, U3.27 (GPA6)
unnamed: J31.3, U3.26 (GPA5)
unnamed: J31.4, U3.25 (GPA4)
unnamed: J31.5, U3.24 (GPA3)
unnamed: J31.6, U3.23 (GPA2)
unnamed: J31.7, U3.22 (GPA1)
unnamed: J31.8, U3.21 (GPA0)

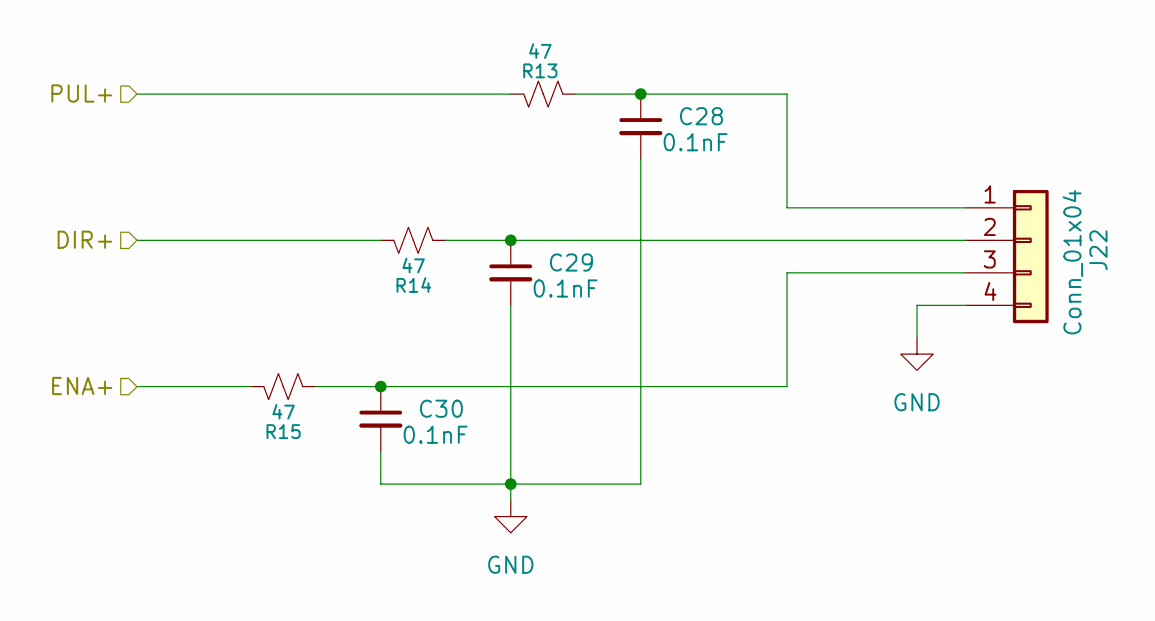
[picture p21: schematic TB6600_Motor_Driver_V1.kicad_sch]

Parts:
C28, C29, C30: 0.1nF; C_0805_2012Metric
J22: Conn_01x04; TerminalBlock_Phoenix_PT-1,5-4-3.5-H_1x04_P3.50mm_Horizontal
R13, R14, R15: 47; R_Axial_DIN0207_L6.3mm_D2.5mm_P7.62mm_Horizontal

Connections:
/TB6600 Motor Driver/DIR+: R14.2; also elsewhere on the board
/TB6600 Motor Driver/ENA+: R15.2; also elsewhere on the board
/TB6600 Motor Driver/PUL+: R13.2; also elsewhere on the board
GND: C28.2, C29.2, C30.2, J22.4; also elsewhere on the board
unnamed: C28.1, J22.1, R13.1
unnamed: C29.1, J22.2, R14.1
unnamed: C30.1, J22.3, R15.1

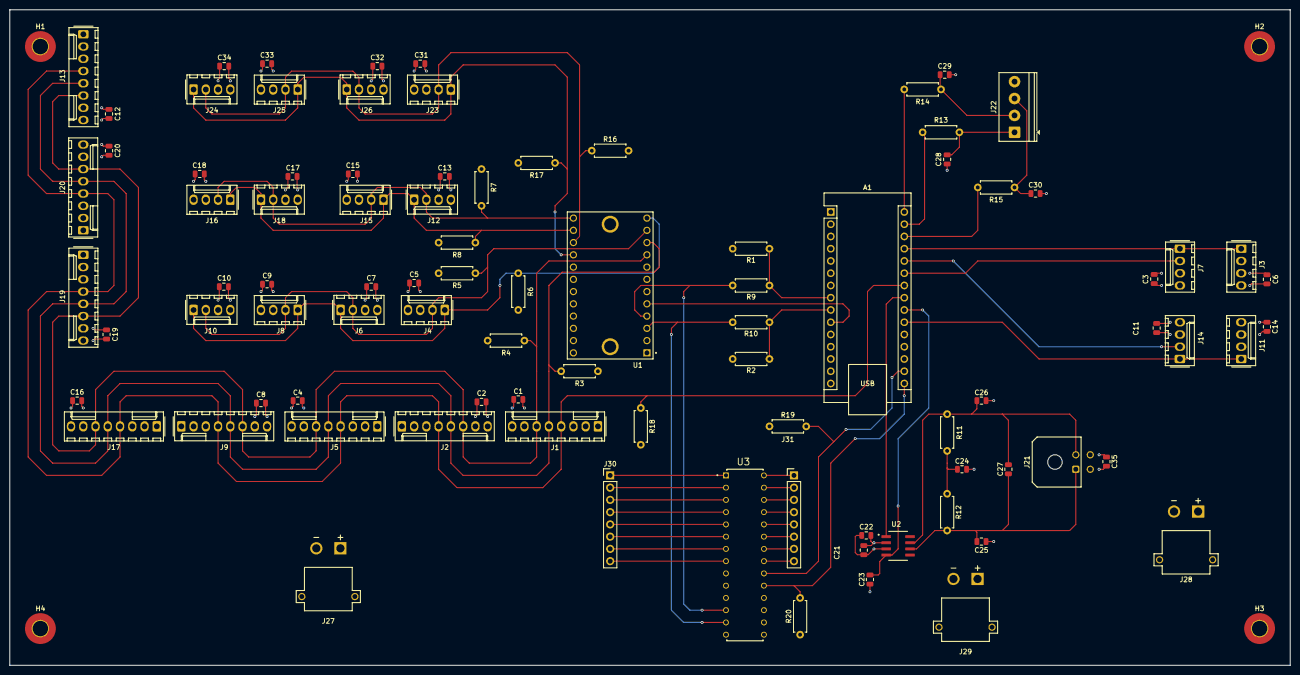
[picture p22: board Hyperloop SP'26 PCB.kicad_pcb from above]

Board: 4 copper layers, 265.4 x 135.9 mm, 94 parts (0 on the bottom side), 51 nets.
